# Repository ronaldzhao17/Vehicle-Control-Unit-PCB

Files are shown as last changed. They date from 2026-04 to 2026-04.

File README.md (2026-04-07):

# Vehicle-Control-Unit-PCB Overview
The Vehicle Control Unit PCB (VCU) is a 4-layer PCB designed for the 2025-2026 Formula SAE Competition EV car (FS-4) at UC Santa Cruz. This board serves as the central low-voltage control system for the vehicle and integrates multiple critical functions into a single platform. The board was designed using KiCAD and printed through JLC PCB.
The board mainly serves these purposes:
1. Brake System Plausibility Device (BSPD) and Main Shutdown Circuit:
2. Electronic Throttle Control: Motor control using position pedal sensor inputs
3. Inertial Measurement Unit: Improves FS-4's traction control
4. System Fault Indication: Traction System Status Indicator, ETC.
## PCB
<div align="center">
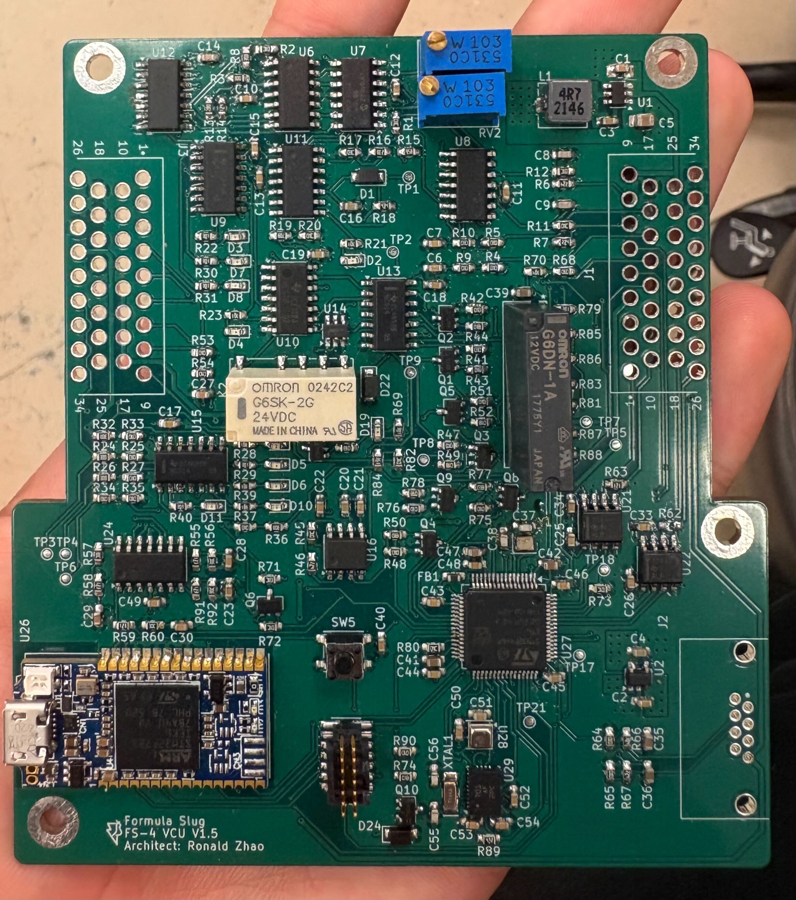
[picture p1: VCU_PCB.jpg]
  
</div>

## Top Layer Signal Diagram
<div align="center">
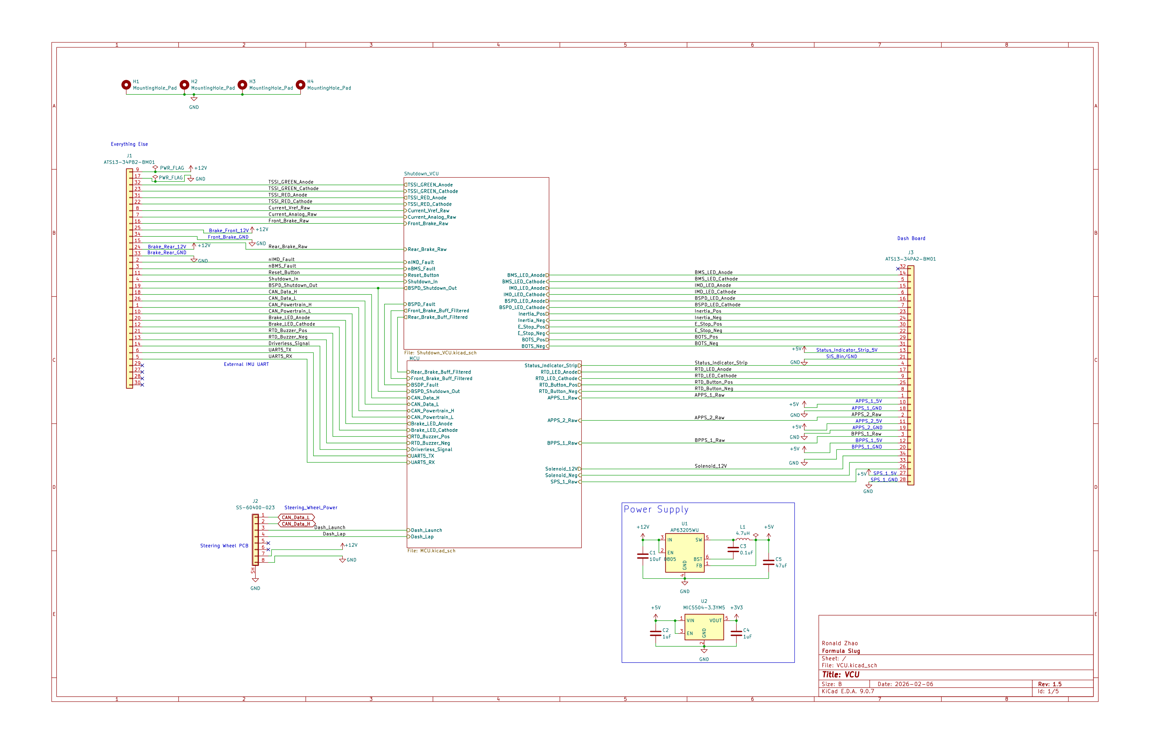
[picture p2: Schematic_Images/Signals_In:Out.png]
  
</div>
The top layer of my schematic is dedicated to present all of the signals inputs and outputs from each connector. It represents a "block diagram" view of the schematic, containing where each of the 60+ signals go.

## BSPD and Shutdown Circuit
<div align="center">
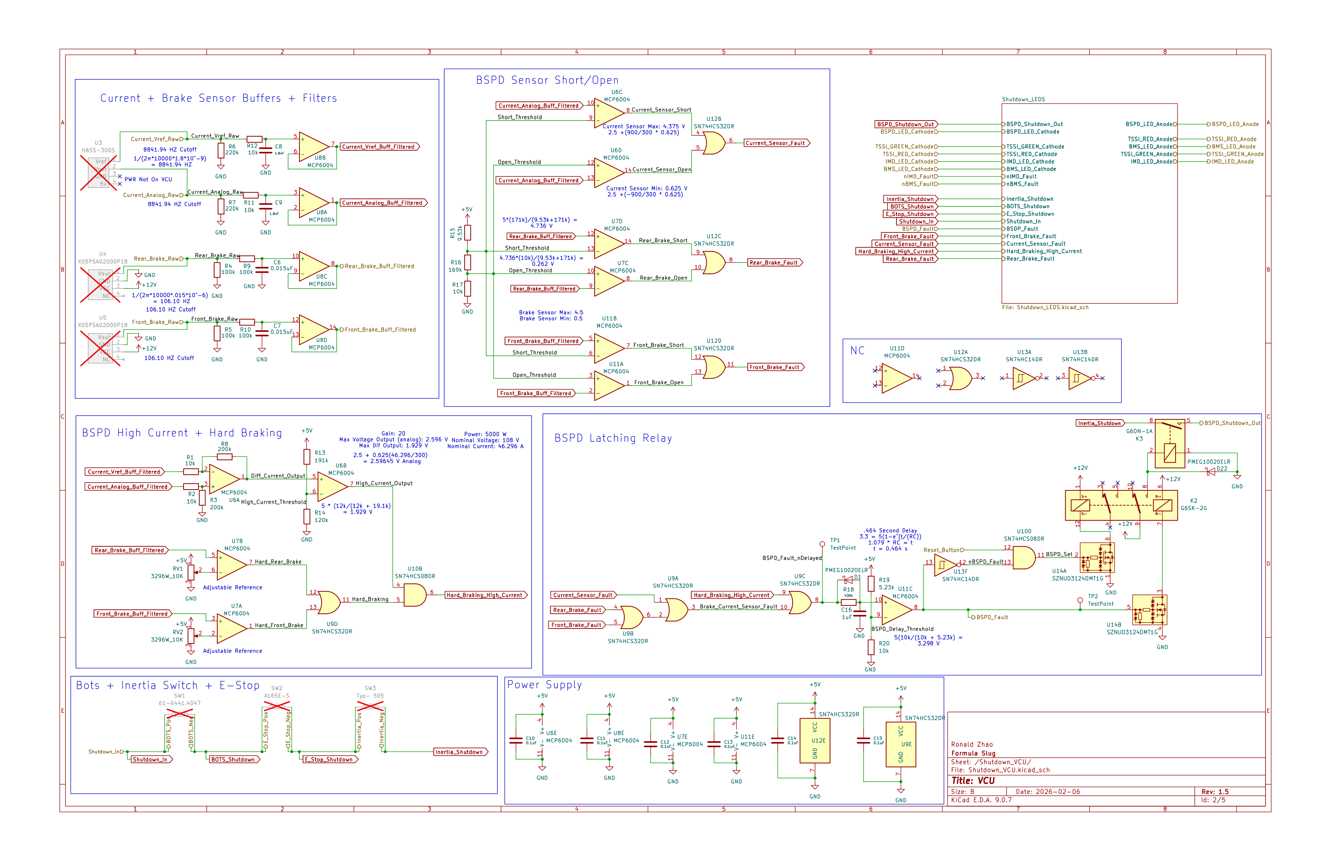
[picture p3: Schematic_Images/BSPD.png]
  
</div>
The brake system plausibility device is a safety mechanism that detects a high current from the motor and active braking. To detect a high current, the output signal from the HASS-300-S current sensor is each filtered to 8841 Hz and buffered. It is then put through a differential amplifier with a gain of 20 in order to obtain a stable, single ended voltage output, as well as a comparator with a voltage threshold based on the reading of the current sensor at our vehicle's nominal current. Similarly, to detect a hard braking, we filter and buffer signals from a pressure sensor for both the front and rear brake. This is compared to a potentiometer we calibrated based on our driver's voltage reading on the pressure sensor while braking. If both of these requirements are fulfilled, then the circuit will output a high, openning our relay connected to the shutdown circuit. Other cases such as the sensor having a short or open circuit also triggers a fault using a series of comparators and logic gates.

## STM32 Microcontroller
<div align="center">
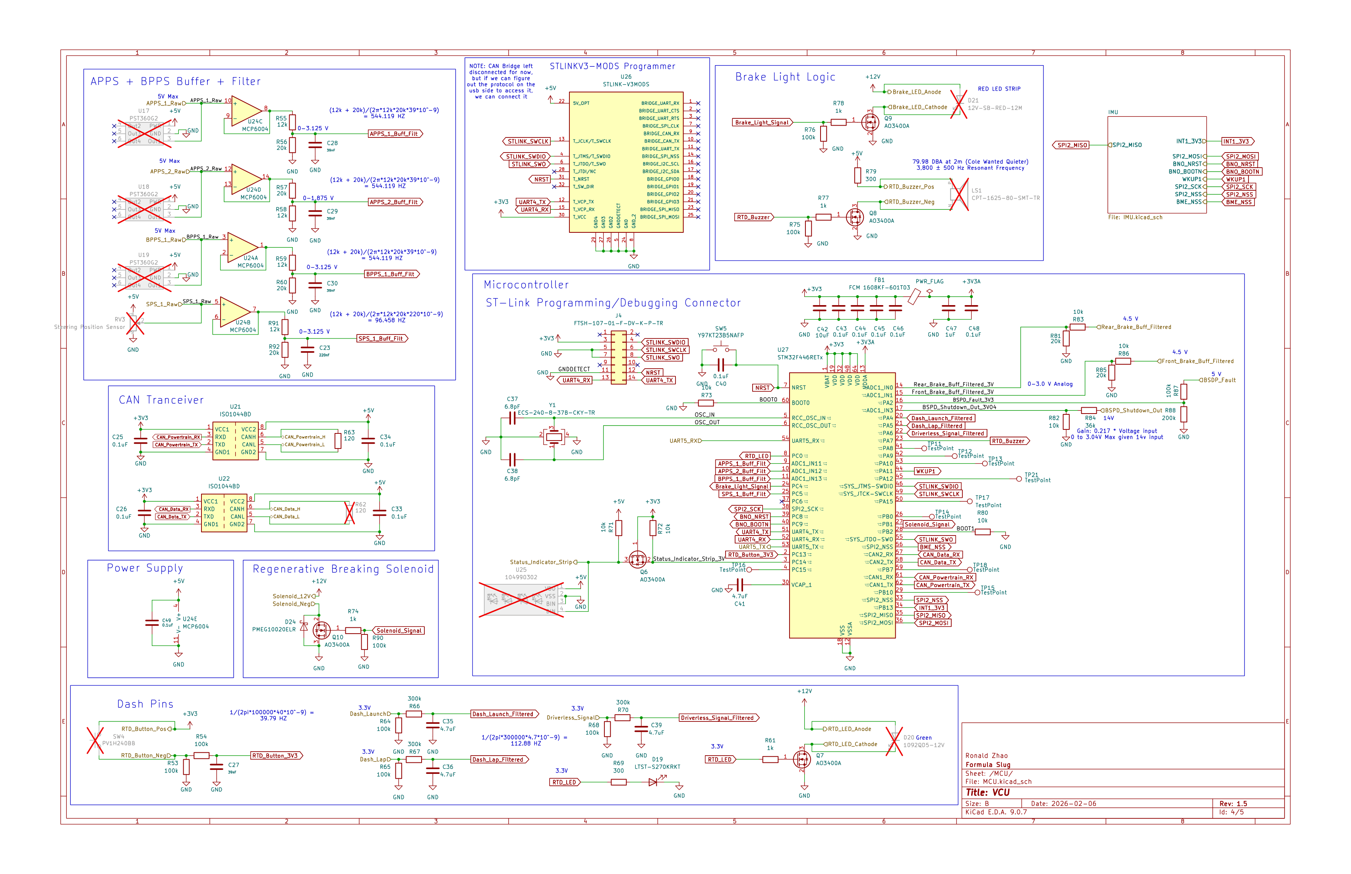
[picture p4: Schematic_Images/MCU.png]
  
</div>
The VCU uses the STM32F446RET6 MCU chip with an external 24 MHz crystal oscillator as its clock, instead previous year's development boards (Nucleos) due to space constraints. The electronic throttle control circuit works by taking in two acceleration pedal position sensor and brake pedal position sensor. This signal is processed by the MCU's firmware and sent through CAN to the motor controller. Other signals going into/out the MCU includes:

- Steering position sensor
- Regenerative Braking Solenoid Signal
- Brake Light
- 2x IMU through SPI and UART
- STLINK V3 MODS Debugger
- Test Points
- Fault Signals

## Inertial Measurement Unit
<div align="center">
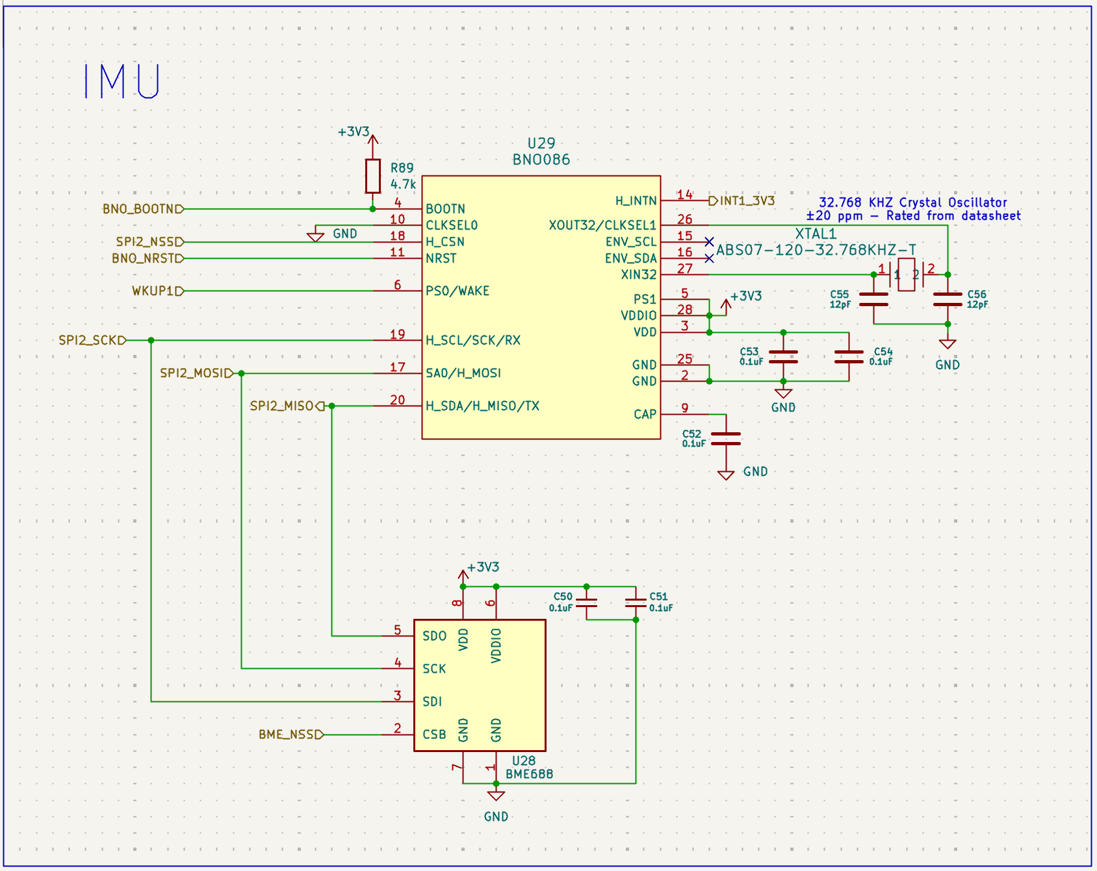
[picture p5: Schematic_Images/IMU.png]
  
</div>
The Inertial Measurement Unit is made up of two sensors to make up the accelerometer, gyroscope, and magnetometer. The IMU uses SPI for its data transfer between the chip and the MCU. Previously our vehicle's traction control was configured to compare the front and rear wheel speed to detect slipping, through our peripheral boards. However, since it requires CAN, the limited bus usage causes the sampling to only be at 100 Hz. This creates a delay and is not practical for quick motor output adjustments. Using the IMU, we can compare both the motor torque output with the car's acceleration (should be proportional) and the steering position sensor's reading with the angular velocity of the car. Since the IMU uses SPI, the sampling rate isn't limited by CAN and has the potential to make precise adjustments.

## Fault Indicators
<div align="center">
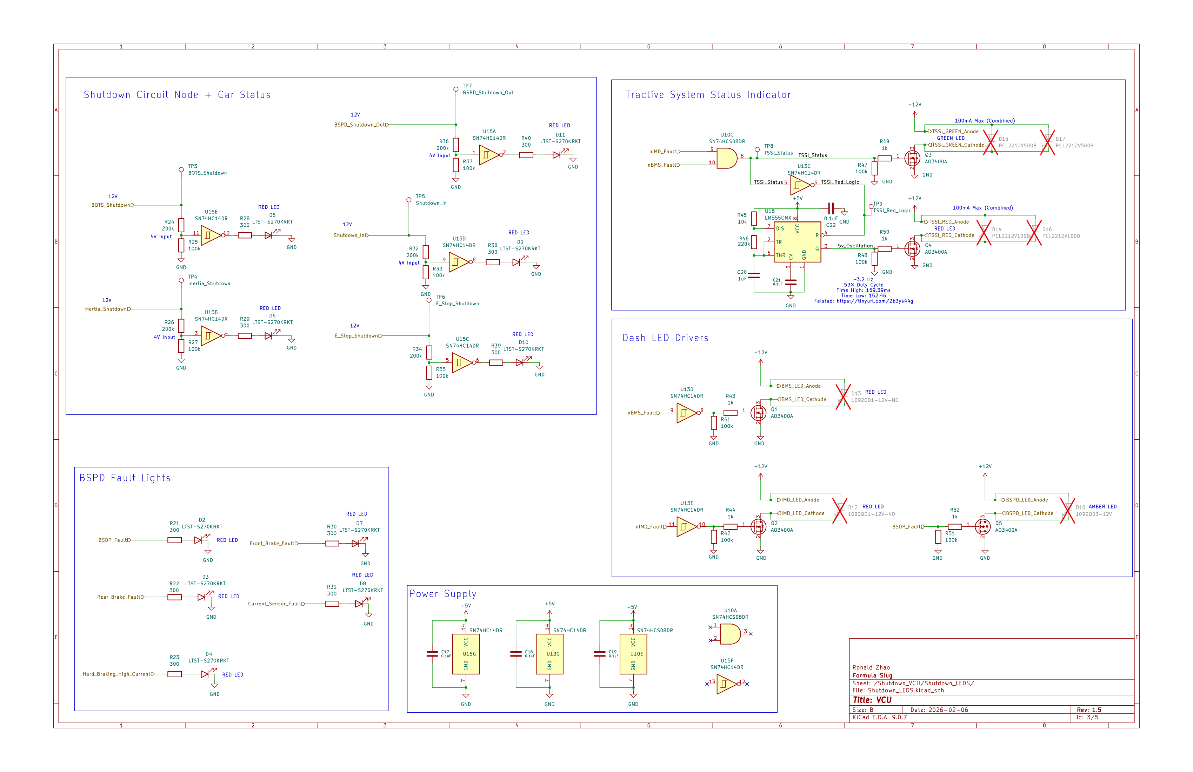
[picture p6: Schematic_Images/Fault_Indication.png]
  
</div>
Fault indicators, such as the Tractive System Status Indicator (TSSI), are required by Formula SAE to signal critical failures in safety-related systems. They also provide a fast method for debugging faults because of their easily accessable test points. These fault lights include:

- IMD
- BMS
- BSPD
- Inertia Switch
- BOTS Switch

## PCB Layout
<div align="center">
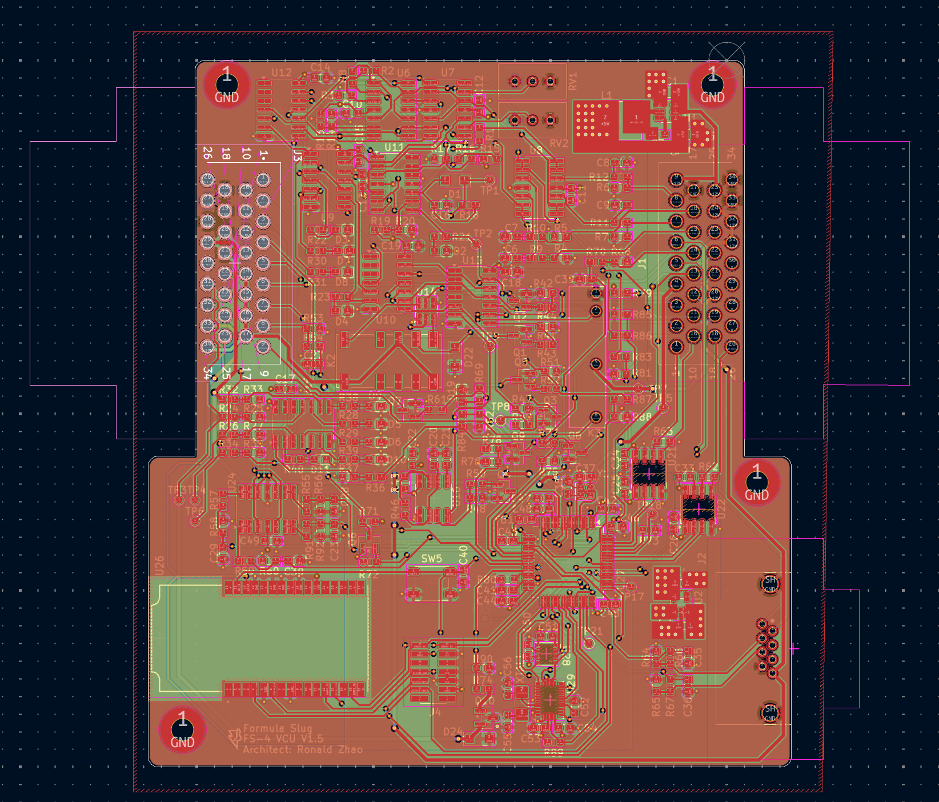
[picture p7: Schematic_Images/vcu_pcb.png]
  
</div>
The layout was done in KiCAD and took almost 6 revisions. It is a 4-layer board with a signal-GND-PWR-signal layer configuration. I started the process by laying out my connectors based on the direction of each respective connectors' signals. Then, I layed out the high speed signals, such as the SPI signal, in a low noise area (far away from DCDC). I kept the traces as short as possible and provided a short return path to reduce the closed loop inductance. The hardest part was placing down my op amps due to the sheer amount of them. To prevent signals crossing, I would often switch the op amp inputs in my schematic. The final design was approved in late February. The end product was a 4x4 inch pcb with over 200 components.

## Soldering, Testing, and Debugging
<div align="center">
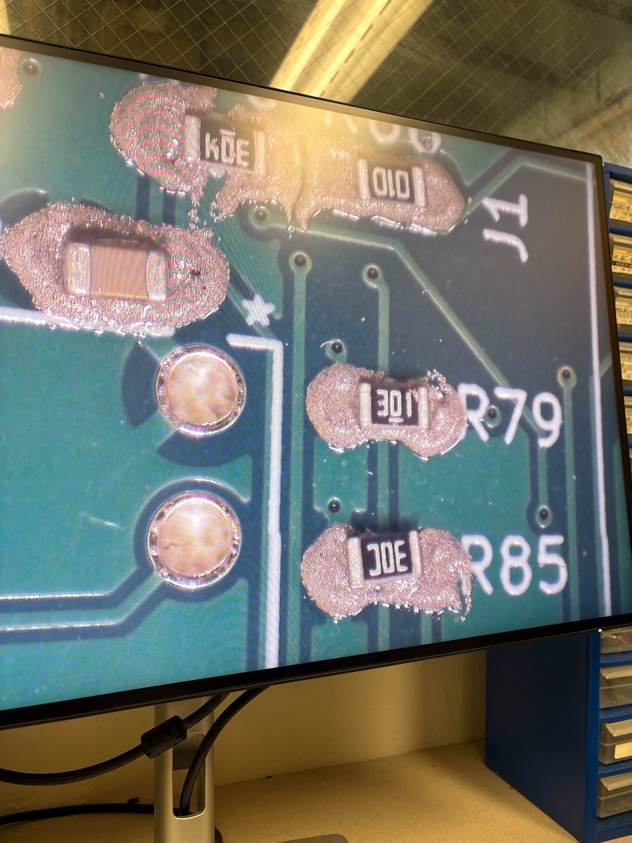
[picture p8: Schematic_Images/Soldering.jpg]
  
</div>
One of the hardest parts of the process was soldering and debugging the board. Almost all of our passive components were 0603 and were entirely hand soldered and the process took over 8 hours. I debugged the board primarily through following my test plan, which you can find here: 

[Test Plan](https://docs.google.com/document/d/1dWHqh_tH-KAfCqI4JE5uINjZ180YYHxUwMFZACGtfho/edit?usp=sharing)

Many of the faults included shorts from the microcontroller and STLINKV3 due to their small pad size. 

## Closing Remarks
This was definitely the biggest, most complex, and my proudest project to date! If you have any questions email me at: ronaldzhao17@gmail.com

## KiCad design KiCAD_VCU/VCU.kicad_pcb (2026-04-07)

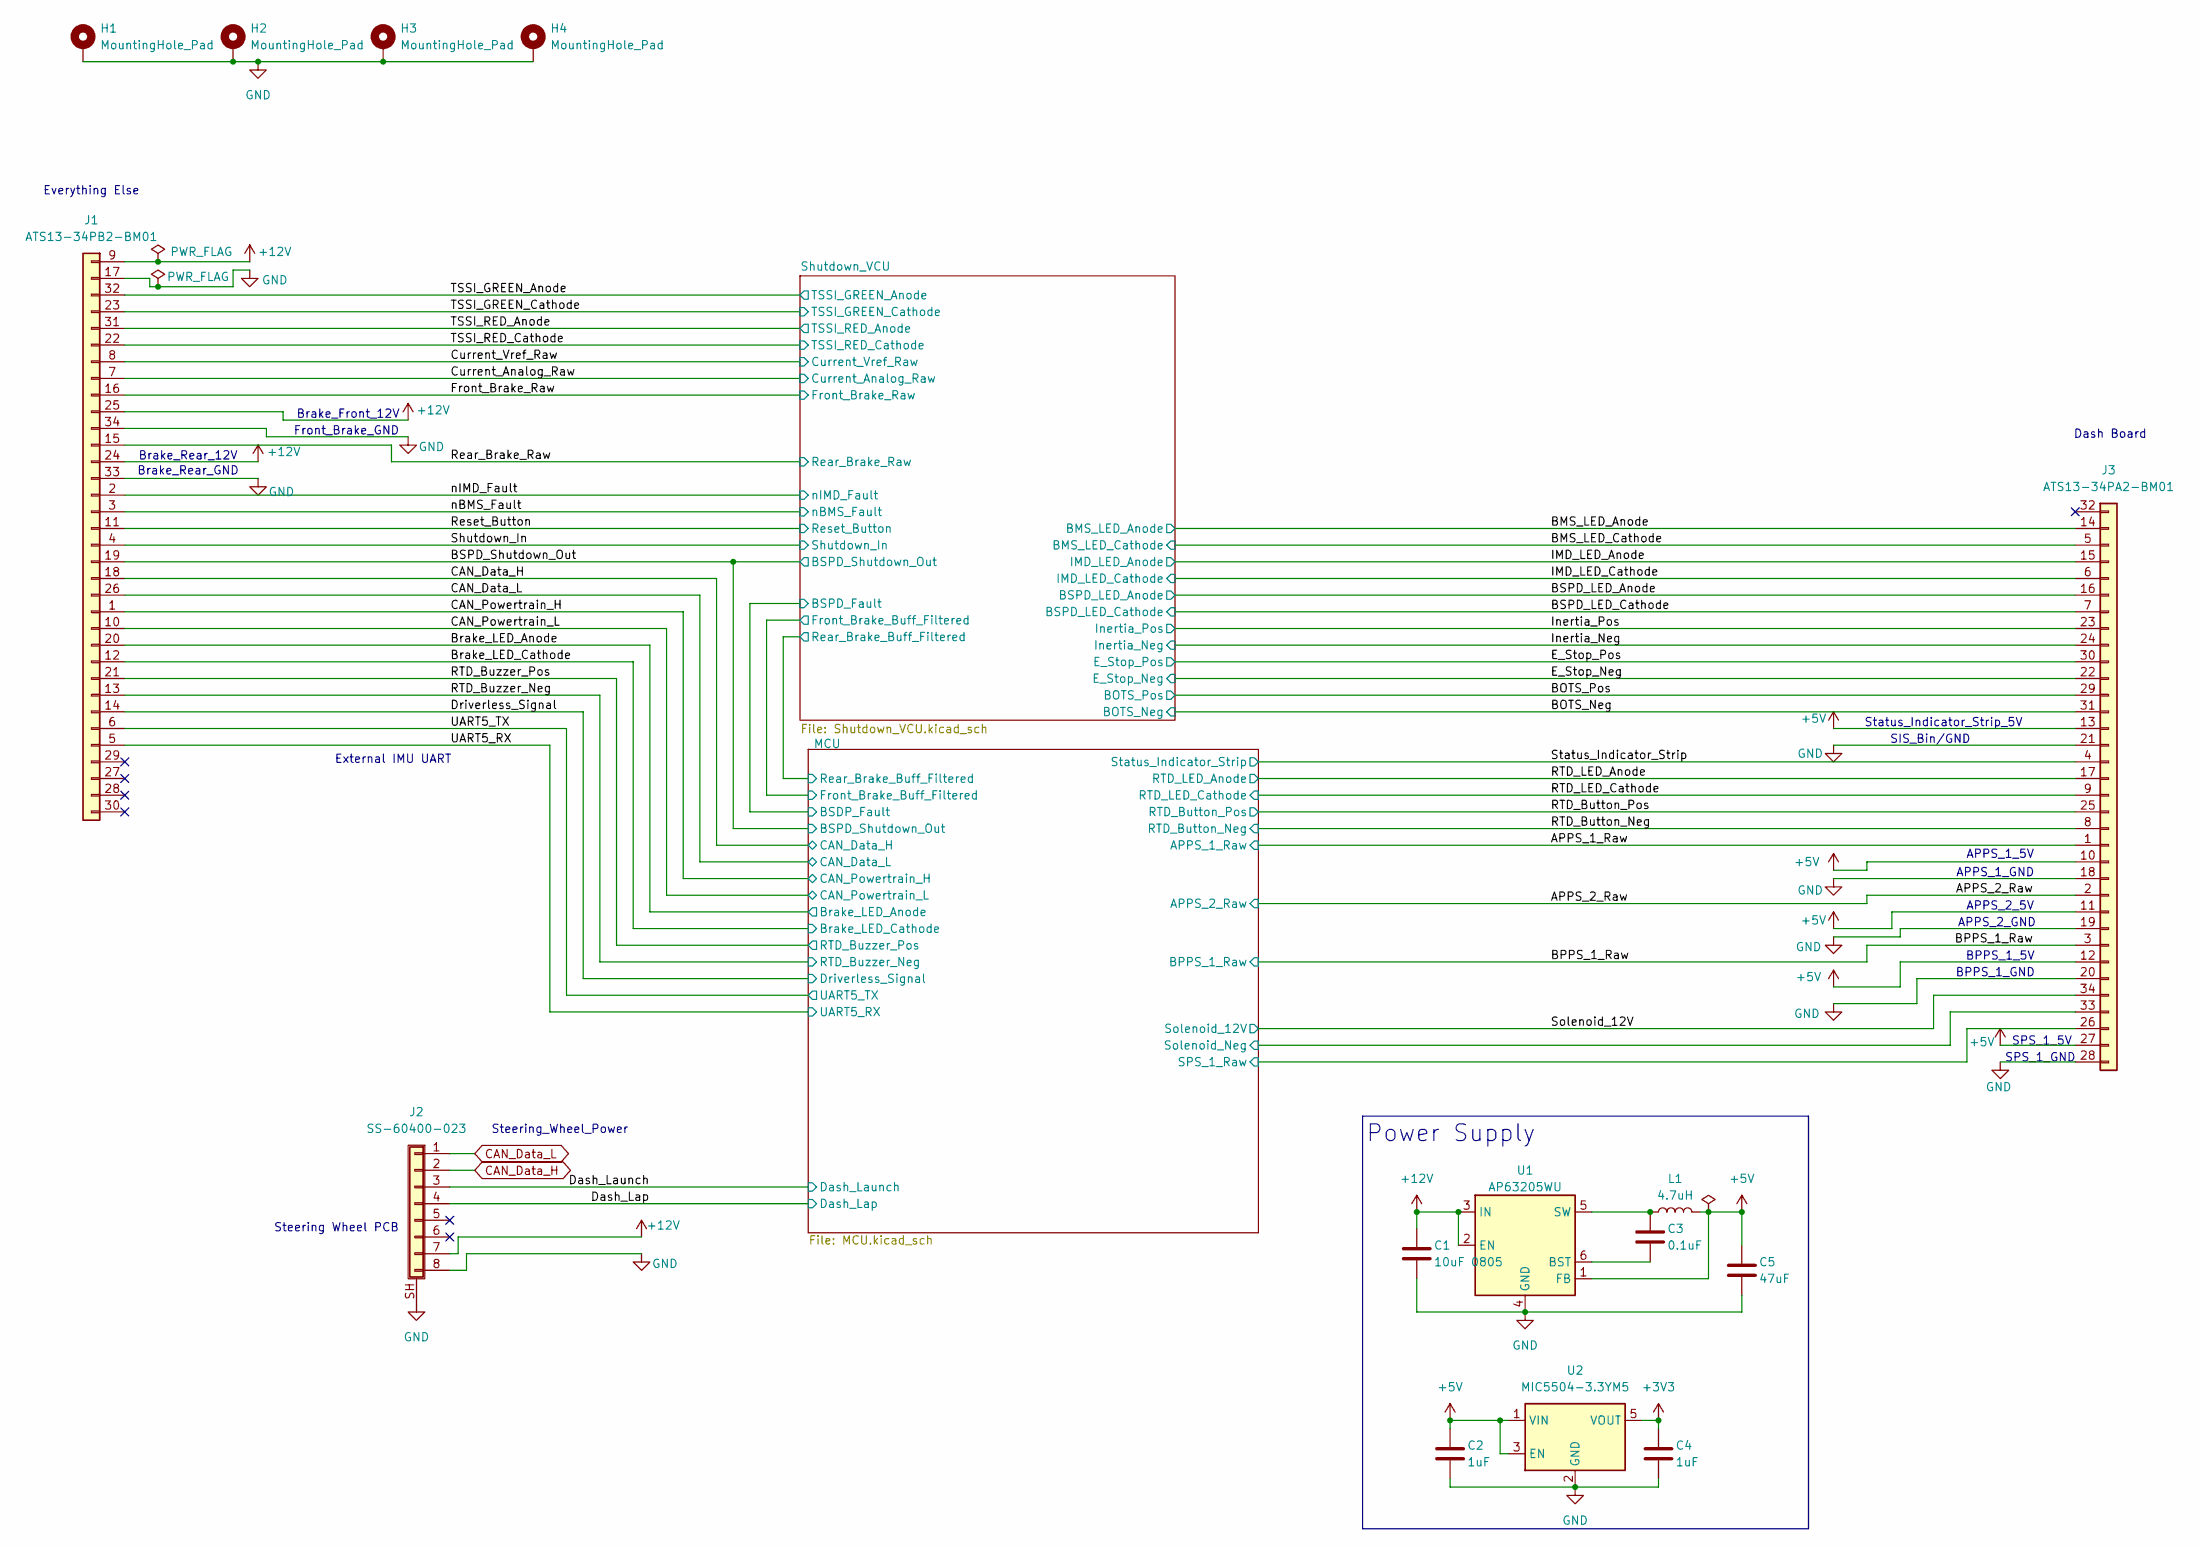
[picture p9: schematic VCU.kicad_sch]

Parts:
C1: 10uF 0805; C_0805_2012Metric_Pad1.18x1.45mm_HandSolder; MFG PN CL21A106KAYNNNE; Digi PN 1276-2891-1-ND
C2, C4: 1uF; C_0603_1608Metric_Pad1.08x0.95mm_HandSolder; MFG PN CC0603JRX7R6BB105; Digi PN 311-3484-1-ND
C3: 0.1uF; C_0603_1608Metric_Pad1.08x0.95mm_HandSolder; MFG PN CC0603JRX7R9BB104; Digi PN 311-1779-1-ND
C5: 47uF; C_0805_2012Metric_Pad1.18x1.45mm_HandSolder; MFG PN CL21A476MQYNNNE; Digi PN 1276-1852-1-ND
H1, H2, H3, H4: MountingHole_Pad; MountingHole_3.2mm_M3_Pad
J1: ATS13-34PB2-BM01; MFG PN ATS13-34PB2-BM01; Digi PN 889-ATS13-34PB2-BM01-ND
J2: SS-60400-023; MFG PN SS-60400-023; Digi PN 380-SS-60400-023-ND
J3: ATS13-34PA2-BM01; MFG PN ATS13-34PA2-BM01; Digi PN 889-ATS13-34PA2-BM01-ND
L1: 4.7uH; L_Bourns_SRP5030T; MFG PN SRP5030TA-4R7M; Digi PN SRP5030TA-4R7MCT-ND
U1: AP63205WU; TSOT-23-6; MFG PN AP63205WU-7; Digi PN AP63205WU-7DICT-ND
U2: MIC5504-3.3YM5; SOT-23-5; MFG PN MIC5504-3.3YM5-TR; Digi PN 576-4764-1-ND

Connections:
+3V3: C4.2, J3.25, U2.5 (VOUT); also elsewhere on the board
+5V: C2.2, C5.2, J3.10, J3.11, J3.12, J3.13, J3.27, L1.2, U1.1 (FB), U2.1 (VIN), U2.3 (EN); also elsewhere on the board
+12V: C1.2, J1.9, J1.20, J1.24, J1.25, J1.31, J1.32, J2.7, J3.14, J3.15, J3.16, J3.17, J3.34, U1.2 (EN), U1.3 (IN); also elsewhere on the board
/APPS_1_Raw: J3.1; also elsewhere on the board
/APPS_2_Raw: J3.2; also elsewhere on the board
/BMS_LED_Cathode: J3.5; also elsewhere on the board
/BPPS_1_Raw: J3.3; also elsewhere on the board
/BSPD_LED_Cathode: J3.7; also elsewhere on the board
/Brake_LED_Cathode: J1.12; also elsewhere on the board
/CAN_Powertrain_H: J1.1; also elsewhere on the board
/CAN_Powertrain_L: J1.10; also elsewhere on the board
/Current_Analog_Raw: J1.7; also elsewhere on the board
/Current_Vref_Raw: J1.8; also elsewhere on the board
/Dash_Lap: J2.4; also elsewhere on the board
/Dash_Launch: J2.3; also elsewhere on the board
/Driverless_Signal: J1.14; also elsewhere on the board
/Front_Brake_Raw: J1.16; also elsewhere on the board
/IMD_LED_Cathode: J3.6; also elsewhere on the board
/MCU/SPS_1_Raw: J3.26; also elsewhere on the board
/MCU/Solenoid_Neg: J3.33; also elsewhere on the board
/RTD_Button_Neg: J3.8; also elsewhere on the board
/RTD_Buzzer_Neg: J1.13; also elsewhere on the board
/RTD_Buzzer_Pos: J1.21; also elsewhere on the board
/RTD_LED_Cathode: J3.9; also elsewhere on the board
/Rear_Brake_Raw: J1.15; also elsewhere on the board
/Reset_Button: J1.11; also elsewhere on the board
/Status_Indicator_Strip: J3.4; also elsewhere on the board
/TSSI_GREEN_Cathode: J1.23; also elsewhere on the board
/TSSI_RED_Cathode: J1.22; also elsewhere on the board
/UART5_RX: J1.5; also elsewhere on the board
/UART5_TX: J1.6; also elsewhere on the board
/nBMS_Fault: J1.3; also elsewhere on the board
/nIMD_Fault: J1.2; also elsewhere on the board
BOTS_Shutdown: J3.30, J3.31; also elsewhere on the board
BSPD_Shutdown_Out: J1.19; also elsewhere on the board
CAN_Data_H: J1.18, J2.2; also elsewhere on the board
CAN_Data_L: J1.26, J2.1; also elsewhere on the board
E_Stop_Shutdown: J3.22, J3.23; also elsewhere on the board
GND: C1.1, C2.1, C4.1, C5.1, H1.1, H2.1, H3.1, H4.1, J1.17, J1.33, J1.34, J2.8, J2.SH (Shield), J3.18, J3.19, J3.20, J3.21, J3.28, U1.4 (GND), U2.2 (GND); also elsewhere on the board
Inertia_Shutdown: J3.24; also elsewhere on the board
unnamed: C3.1, U1.6 (BST)
unnamed: C3.2, L1.1, U1.5 (SW)
Shutdown_In: J1.4, J3.29; also elsewhere on the board

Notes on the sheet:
Brake_Front_12V
External IMU UART
APPS_2_5V
BPPS_1_5V
Front_Brake_GND
APPS_2_GND
Dash Board
Steering Wheel PCB
Steering_Wheel_Power
Status_Indicator_Strip_5V
Everything Else
Brake_Rear_12V
SPS_1_GND
Brake_Rear_GND
Power Supply
APPS_1_GND
SIS_Bin/GND
BPPS_1_GND
APPS_1_5V
SPS_1_5V

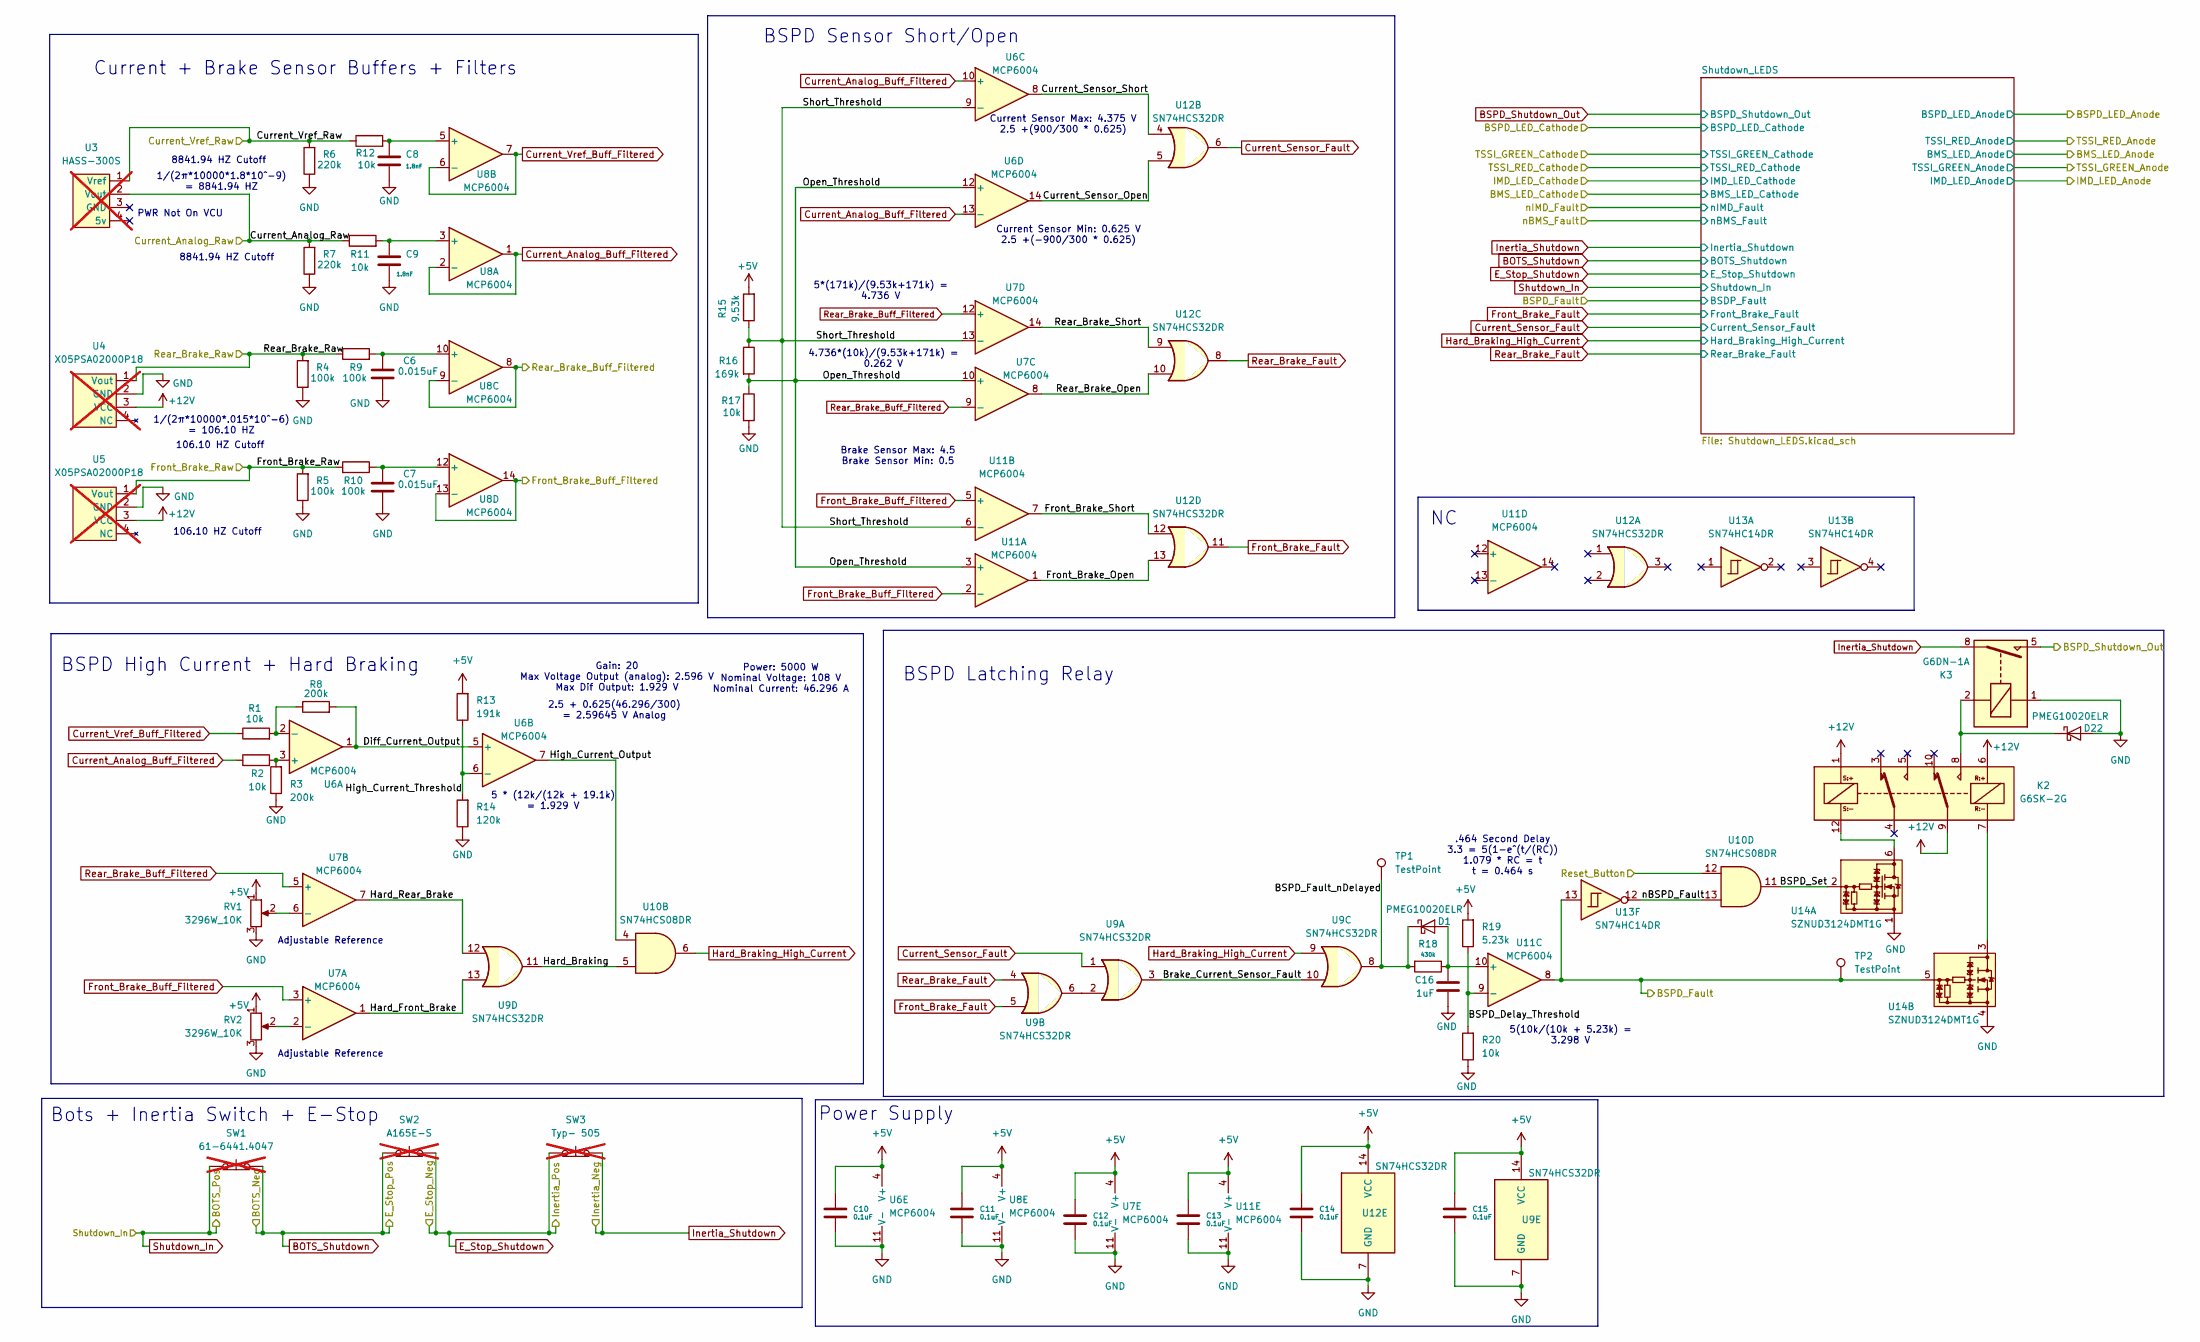
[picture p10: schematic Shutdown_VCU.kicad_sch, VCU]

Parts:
C6, C7: 0.015uF; C_0603_1608Metric_Pad1.08x0.95mm_HandSolder; MFG PN CC0603KRX7R9BB153; Digi PN 311-1430-1-ND
C8, C9: 1.8nF; C_0603_1608Metric_Pad1.08x0.95mm_HandSolder; MFG PN CC0603FRNPO9BN182; Digi PN 13-CC0603FRNPO9BN182CT-ND
C10, C11, C12, C13, C14, C15: 0.1uF; C_0603_1608Metric_Pad1.08x0.95mm_HandSolder; MFG PN CC0603JRX7R9BB104; Digi PN 311-1779-1-ND
C16: 1uF; C_0603_1608Metric_Pad1.08x0.95mm_HandSolder; MFG PN CC0603JRX7R6BB105; Digi PN 311-3484-1-ND
D1, D22: PMEG10020ELR; Nexperia_CFP3_SOD-123W; MFG PN PMEG10020ELR-QX; Digi PN 1727-PMEG10020ELR-QXCT-ND
K2: G6SK-2G; Relay_DPDT_Omron_G6SK-2G; MFG PN G6SK-2G DC24; Digi PN Z12726-ND
K3: G6DN-1A; RELAY_G6DN-1A; MFG PN G6DN-1A DC12; Digi PN Z5440-ND
R1, R2, R11, R12, R17, R20: 10k; R_0603_1608Metric_Pad0.98x0.95mm_HandSolder; MFG PN AC0603FR-0710KL; Digi PN 311-10KLDCT-ND
R3, R8: 200k; R_0603_1608Metric_Pad0.98x0.95mm_HandSolder; MFG PN AC0603FR-07200KL; Digi PN YAG3575CT-ND
R4, R5, R9, R10: 100k; R_0603_1608Metric_Pad0.98x0.95mm_HandSolder; MFG PN AC0603FR-13100KL; Digi PN 13-AC0603FR-13100KLCT-ND
R6, R7: 220k; R_0603_1608Metric_Pad0.98x0.95mm_HandSolder; MFG PN AC0603FR-07220KL; Digi PN YAG3579CT-ND
R13: 191k; R_0603_1608Metric_Pad0.98x0.95mm_HandSolder; MFG PN AC0603FR-07191KL; Digi PN 13-AC0603FR-07191KLCT-ND
R14: 120k; R_0603_1608Metric_Pad0.98x0.95mm_HandSolder; MFG PN AC0603FR-07120KL; Digi PN YAG3562CT-ND
R15: 9.53k; R_0603_1608Metric_Pad0.98x0.95mm_HandSolder; MFG PN AC0603FR-079K53L; Digi PN 13-AC0603FR-079K53LCT-ND
R16: 169k; R_0603_1608Metric_Pad0.98x0.95mm_HandSolder; MFG PN AC0603FR-07169KL; Digi PN 13-AC0603FR-07169KLCT-ND
R18: 430k; R_0603_1608Metric_Pad0.98x0.95mm_HandSolder; MFG PN AC0603FR-07430KL; Digi PN 13-AC0603FR-07430KLCT-ND
R19: 5.23k; R_0603_1608Metric_Pad0.98x0.95mm_HandSolder; MFG PN AC0603FR-075K23L; Digi PN 13-AC0603FR-075K23LCT-ND
RV1, RV2: 3296W_10K; Potentiometer_Bourns_3296W_Vertical; MFG PN 3296W-1-103LF; Digi PN 3296W-103LF-ND
SW1: 61-6441.4047; MFG PN 61-6441.4047; Digi PN 1948-1780-ND; not fitted
SW2: A165E-S; MFG PN A165E-S; Digi PN Z8879-ND; not fitted
SW3: Typ- 505; not fitted
TP1, TP2: TestPoint; TestPoint_Pad_D1.0mm
U3: HASS-300S; MFG PN HASS 300-S; Digi PN 398-1065-ND; not fitted
U4, U5: X05PSA02000P18; not fitted
U6, U7, U8, U11: MCP6004; SOIC-14_3.9x8.7mm_P1.27mm; MFG PN MCP6004T-I/SL; Digi PN MCP6004T-I/SLCT-ND
U9, U12: SN74HCS32DR; SOIC-14_3.9x8.7mm_P1.27mm; MFG PN SN74HCS32DR; Digi PN 296-SN74HCS32DRCT-ND
U10: SN74HCS08DR; SOIC-14_3.9x8.7mm_P1.27mm; MFG PN SN74HCS08DR; Digi PN 296-SN74HCS08DRCT-ND
U13: SN74HC14DR; SOIC-14_3.9x8.7mm_P1.27mm; MFG PN SN74HC14DR; Digi PN 296-1194-1-ND
U14: SZNUD3124DMT1G; SC-74-6_1.55x2.9mm_P0.95mm; MFG PN SZNUD3124DMT1G; Digi PN SZNUD3124DMT1GOSCT-ND

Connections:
+5V: C10.1, C11.1, C12.1, C13.1, C14.1, C15.1, R13.2, R15.2, R19.2, RV1.1, RV2.1, U6.4 (V+), U7.4 (V+), U8.4 (V+), U9.14 (VCC), U11.4 (V+), U12.14 (VCC); also elsewhere on the board
+12V: K2.1, K2.6, K2.9, U4.3 (VCC), U5.3 (VCC); also elsewhere on the board
/Current_Analog_Raw: R7.2, R11.1, U3.2 (Vout); also elsewhere on the board
/Current_Vref_Raw: R6.2, R12.1, U3.1 (Vref); also elsewhere on the board
/Front_Brake_Raw: R5.2, R10.2, U5.1 (Vout); also elsewhere on the board
/MCU/BSDP_Fault: TP2.1, U11.8, U13.13, U14.5; also elsewhere on the board
/Rear_Brake_Raw: R4.2, R9.1, U4.1 (Vout); also elsewhere on the board
/Reset_Button: U10.12; also elsewhere on the board
/Shutdown_VCU/BSPD_Delay_Threshold: R19.1, R20.2, U11.9 (-)
/Shutdown_VCU/BSPD_Fault_nDelayed: D1.1 (K), R18.2, TP1.1, U9.8
/Shutdown_VCU/BSPD_Set: U10.11, U14.2
/Shutdown_VCU/Brake_Current_Sensor_Fault: U9.3, U9.10
/Shutdown_VCU/Current_Sensor_Open: U6.14, U12.5
/Shutdown_VCU/Current_Sensor_Short: U6.8, U12.4
/Shutdown_VCU/Diff_Current_Output: R8.2, U6.1, U6.5 (+)
/Shutdown_VCU/Front_Brake_Open: U11.1, U12.13
/Shutdown_VCU/Front_Brake_Short: U11.7, U12.12
/Shutdown_VCU/Hard_Braking: U9.11, U10.5
/Shutdown_VCU/Hard_Front_Brake: U7.1, U9.13
/Shutdown_VCU/Hard_Rear_Brake: U7.7, U9.12
/Shutdown_VCU/High_Current_Output: U6.7, U10.4
/Shutdown_VCU/High_Current_Threshold: R13.1, R14.2, U6.6 (-)
/Shutdown_VCU/Open_Threshold: R16.2, R17.1, U6.12 (+), U7.10 (+), U11.3 (+)
/Shutdown_VCU/Rear_Brake_Open: U7.8, U12.10
/Shutdown_VCU/Rear_Brake_Short: U7.14, U12.9
/Shutdown_VCU/Short_Threshold: R15.1, R16.1, U6.9 (-), U7.13 (-), U11.6 (-)
/Shutdown_VCU/nBSPD_Fault: U10.13, U13.12
BSPD_Shutdown_Out: K3.5; also elsewhere on the board
Current_Analog_Buff_Filtered: R2.1, U6.10 (+), U6.13 (-), U8.1, U8.2 (-)
Current_Sensor_Fault: U9.1, U12.6; also elsewhere on the board
Current_Vref_Buff_Filtered: R1.1, U8.6 (-), U8.7
Front_Brake_Buff_Filtered: U7.3 (+), U8.13 (-), U8.14, U11.2 (-), U11.5 (+); also elsewhere on the board
Front_Brake_Fault: U9.5, U12.11; also elsewhere on the board
GND: C6.2, C7.2, C8.2, C9.2, C10.2, C11.2, C12.2, C13.2, C14.2, C15.2, C16.1, D22.2 (A), K3.1, R3.1, R4.1, R5.1, R6.1, R7.1, R14.1, R17.2, R20.1, RV1.3, RV2.3, U4.2 (GND), U5.2 (GND), U6.11 (V-), U7.11 (V-), U8.11 (V-), U9.7 (GND), U11.11 (V-), U12.7 (GND), U14.1, U14.4; also elsewhere on the board
Hard_Braking_High_Current: U9.9, U10.6; also elsewhere on the board
Inertia_Shutdown: K3.8, SW3.2 (B); also elsewhere on the board
unnamed: C16.2, D1.2 (A), R18.1, U11.10 (+)
unnamed: D22.1 (K), K2.8, K3.2
unnamed: K2.7, U14.3
unnamed: K2.12, U14.6
unnamed: SW1.2 (B), SW2.1 (A)
unnamed: SW2.2 (B), SW3.1 (A)
unnamed: R2.2, R3.2, U6.3 (+)
unnamed: R1.2, R8.1, U6.2 (-)
unnamed: RV2.2, U7.2 (-)
unnamed: RV1.2, U7.6 (-)
unnamed: C9.1, R11.2, U8.3 (+)
unnamed: C8.1, R12.2, U8.5 (+)
unnamed: C6.1, R9.2, U8.10 (+)
unnamed: C7.1, R10.1, U8.12 (+)
unnamed: U9.2, U9.6
Rear_Brake_Buff_Filtered: U7.5 (+), U7.9 (-), U7.12 (+), U8.8, U8.9 (-); also elsewhere on the board
Rear_Brake_Fault: U9.4, U12.8; also elsewhere on the board

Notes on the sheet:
1/(2π*10000*.015*10^-6) = 106.10 HZ
Power Supply
Current Sensor Max: 4.375 V 2.5 +(900/300 * 0.625)
Gain: 20 Max Voltage Output (analog): 2.596 V Max Dif Output: 1.929 V
Power: 5000 W Nominal Voltage: 108 V Nominal Current: 46.296 A
106.10 HZ Cutoff
Adjustable Reference
1/(2π*10000*1.8*10^-9) = 8841.94 HZ
8841.94 HZ Cutoff
5 * (12k/(12k + 19.1k) = 1.929 V
BSPD Latching Relay
5(10k/(10k + 5.23k) = 3.298 V
Current + Brake Sensor Buffers + Filters
.464 Second Delay 3.3 = 5(1-e^(t/(RC)) 1.079 * RC = t t = 0.464 s
BSPD Sensor Short/Open
2.5 + 0.625(46.296/300) = 2.59645 V Analog
4.736*(10k)/(9.53k+171k) = 0.262 V
Brake Sensor Max: 4.5 Brake Sensor Min: 0.5
Current Sensor Min: 0.625 V 2.5 +(-900/300 * 0.625)
Bots + Inertia Switch + E-Stop
5*(171k)/(9.53k+171k) = 4.736 V
BSPD High Current + Hard Braking
PWR Not On VCU

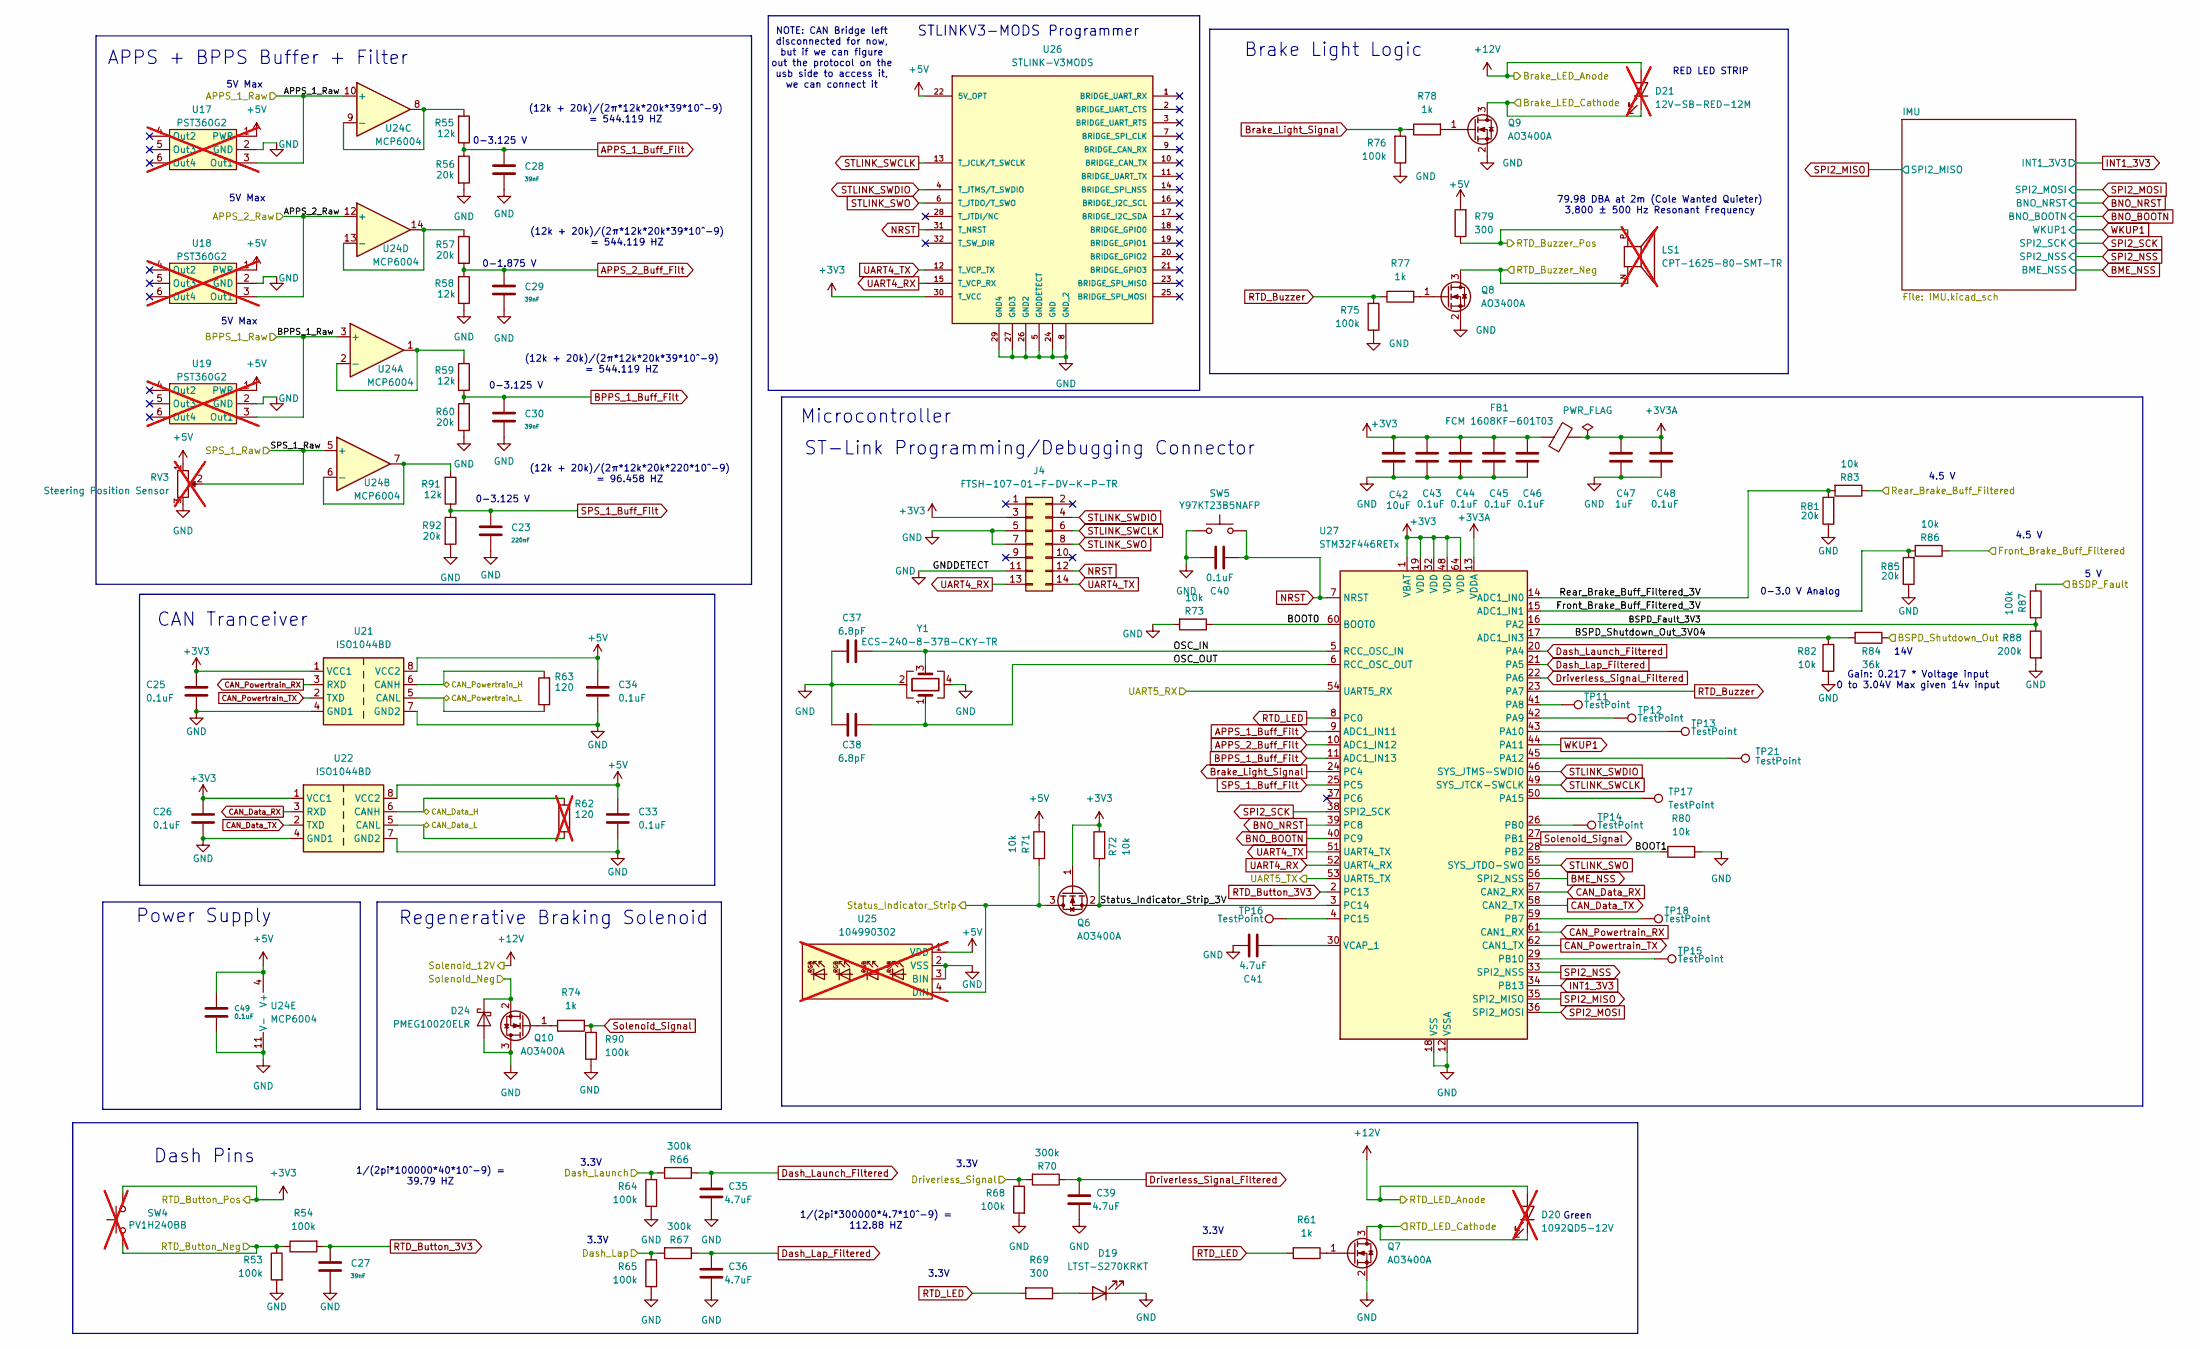
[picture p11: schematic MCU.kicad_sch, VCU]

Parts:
C23: 220nF; C_0603_1608Metric_Pad1.08x0.95mm_HandSolder; MFG PN CC0603KRX7R8BB224; Digi PN 311-1803-1-ND
C25, C26, C33, C34, C40, C43, C44, C45, C46, C48, C49: 0.1uF; C_0603_1608Metric_Pad1.08x0.95mm_HandSolder; MFG PN CC0603JRX7R9BB104; Digi PN 311-1779-1-ND
C27, C28, C29, C30: 39nF; C_0603_1608Metric_Pad1.08x0.95mm_HandSolder; MFG PN CC0603JRX7R9BB393; Digi PN 13-CC0603JRX7R9BB393CT-ND
C35, C36, C39, C41: 4.7uF; C_0603_1608Metric_Pad1.08x0.95mm_HandSolder; MFG PN CL10A475KL8NRNC; Digi PN 1276-6794-1-ND
C37, C38: 6.8pF; C_0603_1608Metric_Pad1.08x0.95mm_HandSolder; MFG PN CC0603DRNPO9BN6R8; Digi PN 311-3874-1-ND
C42: 10uF; C_0603_1608Metric_Pad1.08x0.95mm_HandSolder; MFG PN CL10A106KO8NQNC; Digi PN 1276-CL10A106KO8NQNCCT-ND
C47: 1uF; C_0603_1608Metric_Pad1.08x0.95mm_HandSolder; MFG PN CC0603JRX7R6BB105; Digi PN 311-3484-1-ND
D19: LTST-S270KRKT; LED_0603_1608Metric_Pad1.05x0.95mm_HandSolder; MFG PN LTST-S270KRKT; Digi PN 160-1479-1-ND
D20: 1092QD5-12V; MFG PN 1092QD5-12V; Digi PN 1092QD5-12V-ND; not fitted
D21: 12V-SB-RED-12M; MFG PN 12V-SB-RED-12M; Digi PN 1647-12V-SB-RED-12MCT-ND; not fitted
D24: PMEG10020ELR; Nexperia_CFP3_SOD-123W; MFG PN PMEG10020ELR-QX; Digi PN 1727-PMEG10020ELR-QXCT-ND
FB1: FCM 1608KF-601T03; L_0603_1608Metric_Pad1.05x0.95mm_HandSolder; MFG PN FCM 1608KF-601T03; Digi PN 4816-FCM1608KF-601T03CT-ND
J4: FTSH-107-01-F-DV-K-P-TR; PinHeader_2x07_P1.27mm_Vertical_SMD; MFG PN FTSH-107-01-F-DV-K-P-TR; Digi PN SAM13170CT-ND
LS1: CPT-1625-80-SMT-TR; MFG PN AI-3238-TF-LW140-R; Digi PN 668-1277-ND; not fitted
Q6, Q7, Q8, Q9, Q10: AO3400A; SOT-23; MFG PN AO3400A; Digi PN 785-1000-1-ND
R53, R54, R64, R65, R68, R75, R76, R87, R90: 100k; R_0603_1608Metric_Pad0.98x0.95mm_HandSolder; MFG PN AC0603FR-13100KL; Digi PN 13-AC0603FR-13100KLCT-ND
R55, R58, R59, R91: 12k; R_0603_1608Metric_Pad0.98x0.95mm_HandSolder; MFG PN AC0603FR-1012KL; Digi PN 13-AC0603FR-1012KLCT-ND
R56, R57, R60, R81, R85, R92: 20k; R_0603_1608Metric_Pad0.98x0.95mm_HandSolder; MFG PN AC0603FR-0720KL; Digi PN YAG3577CT-ND
R61, R74, R77, R78: 1k; R_0603_1608Metric_Pad0.98x0.95mm_HandSolder; MFG PN RC0603FR-071KL; Digi PN 311-1.00KHRCT-ND
R62: 120; R_0603_1608Metric_Pad0.98x0.95mm_HandSolder; MFG PN AC0603FR-07120RL; Digi PN YAG3563CT-ND; not fitted
R63: 120; R_0603_1608Metric_Pad0.98x0.95mm_HandSolder; MFG PN AC0603FR-07120RL; Digi PN YAG3563CT-ND
R66, R67, R70: 300k; R_0603_1608Metric_Pad0.98x0.95mm_HandSolder; MFG PN AC0603FR-07300KL; Digi PN 13-AC0603FR-07300KLCT-ND
R69, R79: 300; R_0603_1608Metric_Pad0.98x0.95mm_HandSolder; MFG PN AC0603FR-07300RL; Digi PN YAG5330CT-ND
R71, R72, R73, R80, R82, R83, R86: 10k; R_0603_1608Metric_Pad0.98x0.95mm_HandSolder; MFG PN AC0603FR-0710KL; Digi PN 311-10KLDCT-ND
R84: 36k; R_0603_1608Metric_Pad0.98x0.95mm_HandSolder; MFG PN AC0603FR-0736KL; Digi PN 13-AC0603FR-0736KLCT-ND
R88: 200k; R_0603_1608Metric_Pad0.98x0.95mm_HandSolder; MFG PN AC0603FR-07200KL; Digi PN YAG3575CT-ND
RV3: Steering Position Sensor; not fitted
SW4: PV1H240BB; SW_SPST_PTS647_Sx38; MFG PN PV1H240BB; Digi PN EG5277-ND; not fitted
SW5: Y97KT23B5NAFP; SW_SPST_PTS647_Sx38; MFG PN Y97KT23B5NAFP; Digi PN 108-Y97KT23B5NAFPCT-ND
TP11, TP12, TP13, TP14, TP15, TP16, TP17, TP18, TP21: TestPoint; TestPoint_Pad_D1.0mm
U17, U18, U19: PST360G2; MFG PN PST360G2-1A-C0000-ERA360-05K; Digi PN 1993-1011-ND; not fitted
U21, U22: ISO1044BD; SOIC-8_ISO1044BD; MFG PN ISO1044BDR; Digi PN 296-ISO1044BDRCT-ND
U24: MCP6004; SOIC-14_3.9x8.7mm_P1.27mm; MFG PN MCP6004T-I/SL; Digi PN MCP6004T-I/SLCT-ND
U25: 104990302; MFG PN 104990302; Digi PN 1597-1485-ND; not fitted
U26: STLINK-V3MODS; MODULE_STLINK-V3MODS; PARTREV 1; Digi PN 497-STLINK-V3MODS-ND
U27: STM32F446RETx; LQFP-64_10x10mm_P0.5mm; MFG PN STM32F446RET6; Digi PN 497-15376-ND
Y1: ECS-240-8-37B-CKY-TR; Crystal_SMD_2016-4Pin_2.0x1.6mm; MFG PN ECS-240-8-37B-CKY-TR; Digi PN XC3063CT-ND

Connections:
+3V3: C25.1, C26.1, C42.2, C43.1, C44.1, C45.1, C46.1, FB1.1, J4.3, Q6.1 (G), R72.2, SW4.2, U21.1 (VCC1), U22.1 (VCC1), U26.30 (T_VCC), U27.1 (VBAT), U27.19 (VDD), U27.32 (VDD), U27.48 (VDD), U27.64 (VDD); also elsewhere on the board
+3V3A: C47.1, C48.1, FB1.2, U27.13 (VDDA)
+5V: C33.1, C34.1, C49.1, R71.1, R79.2, RV3.1, U17.1 (PWR), U18.1 (PWR), U19.1 (PWR), U21.8 (VCC2), U22.8 (VCC2), U24.4 (V+), U25.1 (VDD), U26.22 (5V_OPT); also elsewhere on the board
/APPS_1_Raw: U17.3 (Out1), U24.10 (+); also elsewhere on the board
/APPS_2_Raw: U18.3 (Out1), U24.12 (+); also elsewhere on the board
/BPPS_1_Raw: U19.3 (Out1), U24.3 (+); also elsewhere on the board
/Brake_LED_Cathode: D21.1 (K), Q9.3 (D); also elsewhere on the board
/CAN_Powertrain_H: R63.2, U21.6 (CANH); also elsewhere on the board
/CAN_Powertrain_L: R63.1, U21.5 (CANL); also elsewhere on the board
/Dash_Lap: R65.1, R67.2; also elsewhere on the board
/Dash_Launch: R64.1, R66.2; also elsewhere on the board
/Driverless_Signal: R68.1, R70.2; also elsewhere on the board
/MCU/BOOT0: R73.1, U27.60 (BOOT0)
/MCU/BOOT1: R80.1, U27.28 (PB2)
/MCU/BSDP_Fault: R87.1; also elsewhere on the board
/MCU/BSPD_Fault_3V3: R87.2, R88.1, U27.16 (PA2)
/MCU/BSPD_Shutdown_Out_3V04: R82.1, R84.2, U27.17 (ADC1_IN3)
/MCU/Front_Brake_Buff_Filtered_3V: R85.2, R86.2, U27.15 (ADC1_IN1)
/MCU/OSC_IN: C37.1, U27.5 (RCC_OSC_IN), Y1.3
/MCU/OSC_OUT: C38.1, U27.6 (RCC_OSC_OUT), Y1.1
/MCU/Rear_Brake_Buff_Filtered_3V: R81.2, R83.2, U27.14 (ADC1_IN0)
/MCU/SPS_1_Raw: RV3.2, U24.5 (+); also elsewhere on the board
/MCU/Solenoid_Neg: D24.1 (K), Q10.2 (S); also elsewhere on the board
/MCU/Status_Indicator_Strip_3V: Q6.2 (S), R72.1, U27.3 (PC14)
/RTD_Button_Neg: R53.1, R54.1, SW4.1; also elsewhere on the board
/RTD_Buzzer_Neg: LS1.N, Q8.3 (D); also elsewhere on the board
/RTD_Buzzer_Pos: LS1.P, R79.1; also elsewhere on the board
/RTD_LED_Cathode: D20.1 (K), Q7.3 (D); also elsewhere on the board
/Status_Indicator_Strip: Q6.3 (D), R71.2, U25.4 (DIN); also elsewhere on the board
/UART5_RX: U27.54 (UART5_RX); also elsewhere on the board
/UART5_TX: U27.53 (UART5_TX); also elsewhere on the board
APPS_1_Buff_Filt: C28.1, R55.1, R56.1, U27.9 (ADC1_IN11)
APPS_2_Buff_Filt: C29.1, R57.2, R58.2, U27.10 (ADC1_IN12)
BME_NSS: U27.56 (SPI2_NSS); also elsewhere on the board
BNO_BOOTN: U27.40 (PC9); also elsewhere on the board
BNO_NRST: U27.39 (PC8); also elsewhere on the board
BPPS_1_Buff_Filt: C30.1, R59.1, R60.1, U27.11 (ADC1_IN13)
BSPD_Shutdown_Out: R84.1; also elsewhere on the board
Brake_Light_Signal: R76.2, R78.1, U27.24 (PC4)
CAN_Data_H: R62.2, U22.6 (CANH); also elsewhere on the board
CAN_Data_L: R62.1, U22.5 (CANL); also elsewhere on the board
CAN_Data_RX: U22.3 (RXD), U27.57 (CAN2_RX)
CAN_Data_TX: U22.2 (TXD), U27.58 (CAN2_TX)
CAN_Powertrain_RX: U21.3 (RXD), U27.61 (CAN1_RX)
CAN_Powertrain_TX: U21.2 (TXD), U27.62 (CAN1_TX)
Dash_Lap_Filtered: C36.1, R67.1, U27.21 (PA5)
Dash_Launch_Filtered: C35.1, R66.1, U27.20 (PA4)
Driverless_Signal_Filtered: C39.1, R70.1, U27.22 (PA6)
Front_Brake_Buff_Filtered: R86.1; also elsewhere on the board
GND: C23.2, C25.2, C26.2, C27.2, C28.2, C29.2, C30.2, C33.2, C34.2, C35.2, C36.2, C37.2, C38.2, C39.2, C40.1, C41.1, C42.1, C43.2, C44.2, C45.2, C46.2, C47.2, C48.2, C49.2, D19.1 (K), D24.2 (A), J4.5, J4.7, J4.11, Q7.2 (S), Q8.2 (S), Q9.2 (S), Q10.3 (D), R53.2, R56.2, R58.1, R60.2, R64.2, R65.2, R68.2, R73.2, R75.1, R76.1, R80.2, R81.1, R82.2, R85.1, R88.2, R90.1, R92.2, RV3.3, SW5.1, U17.2 (GND), U18.2 (GND), U19.2 (GND), U21.4 (GND1), U21.7 (GND2), U22.4 (GND1), U22.7 (GND2), U24.11 (V-), U25.2 (VSS), U25.3 (BIN), U26.5 (GNDDETECT), U26.8 (GND_2), U26.24 (GND), U26.26 (GND2), U26.27 (GND3), U26.29 (GND4), U27.12 (VSSA), U27.18 (VSS), U27.31 (VSS), U27.47 (VSS), U27.63 (VSS), Y1.2, Y1.4; also elsewhere on the board
INT1_3V3: U27.34 (PB13); also elsewhere on the board
NRST: C40.2, J4.12, SW5.2, U26.31 (T_NRST), U27.7 (NRST)
unnamed: D19.2 (A), R69.1
unnamed: D20.2 (A), D21.2 (A)
unnamed: Q7.1 (G), R61.1
unnamed: Q8.1 (G), R77.2
unnamed: Q9.1 (G), R78.2
unnamed: Q10.1 (G), R74.1
unnamed: R59.2, U24.1, U24.2 (-)
unnamed: R91.2, U24.6 (-), U24.7
unnamed: R55.2, U24.8, U24.9 (-)
unnamed: R57.1, U24.13 (-), U24.14
unnamed: TP11.1, U27.41 (PA8)
unnamed: TP12.1, U27.42 (PA9)
unnamed: TP13.1, U27.43 (PA10)
unnamed: TP21.1, U27.45 (PA12)
unnamed: TP17.1, U27.50 (PA15)
unnamed: TP14.1, U27.26 (PB0)
unnamed: TP18.1, U27.59 (PB7)
unnamed: TP15.1, U27.29 (PB10)
unnamed: TP16.1, U27.4 (PC15)
unnamed: C41.2, U27.30 (VCAP_1)
RTD_Button_3V3: C27.1, R54.2, U27.2 (PC13)
RTD_Buzzer: R75.2, R77.1, U27.23 (PA7)
RTD_LED: R61.2, R69.2, U27.8 (PC0)
Rear_Brake_Buff_Filtered: R83.1; also elsewhere on the board
SPI2_MISO: U27.35 (SPI2_MISO); also elsewhere on the board
SPI2_MOSI: U27.36 (SPI2_MOSI); also elsewhere on the board
SPI2_NSS: U27.33 (SPI2_NSS); also elsewhere on the board
SPI2_SCK: U27.38 (SPI2_SCK); also elsewhere on the board
SPS_1_Buff_Filt: C23.1, R91.1, R92.1, U27.25 (PC5)
STLINK_SWCLK: J4.6, U26.13 (T_JCLK/T_SWCLK), U27.49 (SYS_JTCK-SWCLK)
STLINK_SWDIO: J4.4, U26.4 (T_JTMS/T_SWDIO), U27.46 (SYS_JTMS-SWDIO)
STLINK_SWO: J4.8, U26.6 (T_JTDO/T_SWO), U27.55 (SYS_JTDO-SWO)
Solenoid_Signal: R74.2, R90.2, U27.27 (PB1)
UART4_RX: J4.13, U26.15 (T_VCP_RX), U27.52 (UART4_RX)
UART4_TX: J4.14, U26.12 (T_VCP_TX), U27.51 (UART4_TX)
WKUP1: U27.44 (PA11); also elsewhere on the board

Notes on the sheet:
3.3V
(12k + 20k)/(2π*12k*20k*39*10^-9) = 544.119 HZ
1/(2pi*100000*40*10^-9) = 39.79 HZ
STLINKV3-MODS Programmer
RED LED STRIP
0-3.125 V
0-1.875 V
Dash Pins
CAN Tranceiver
Brake Light Logic
4.5 V
5V Max
0-3.0 V Analog
Green
ST-Link Programming/Debugging Connector
(12k + 20k)/(2π*12k*20k*220*10^-9) = 96.458 HZ
Regenerative Braking Solenoid
NOTE: CAN Bridge left disconnected for now, but if we can figure out the protocol on the usb side to access it, we can connect it
79.98 DBA at 2m (Cole Wanted Quieter) 3,800 ± 500 Hz Resonant Frequency
1/(2pi*300000*4.7*10^-9) = 112.88 HZ
5V Max
APPS + BPPS Buffer + Filter
5 V
Power Supply
14V
Gain: 0.217 * Voltage input 0 to 3.04V Max given 14v input
Microcontroller

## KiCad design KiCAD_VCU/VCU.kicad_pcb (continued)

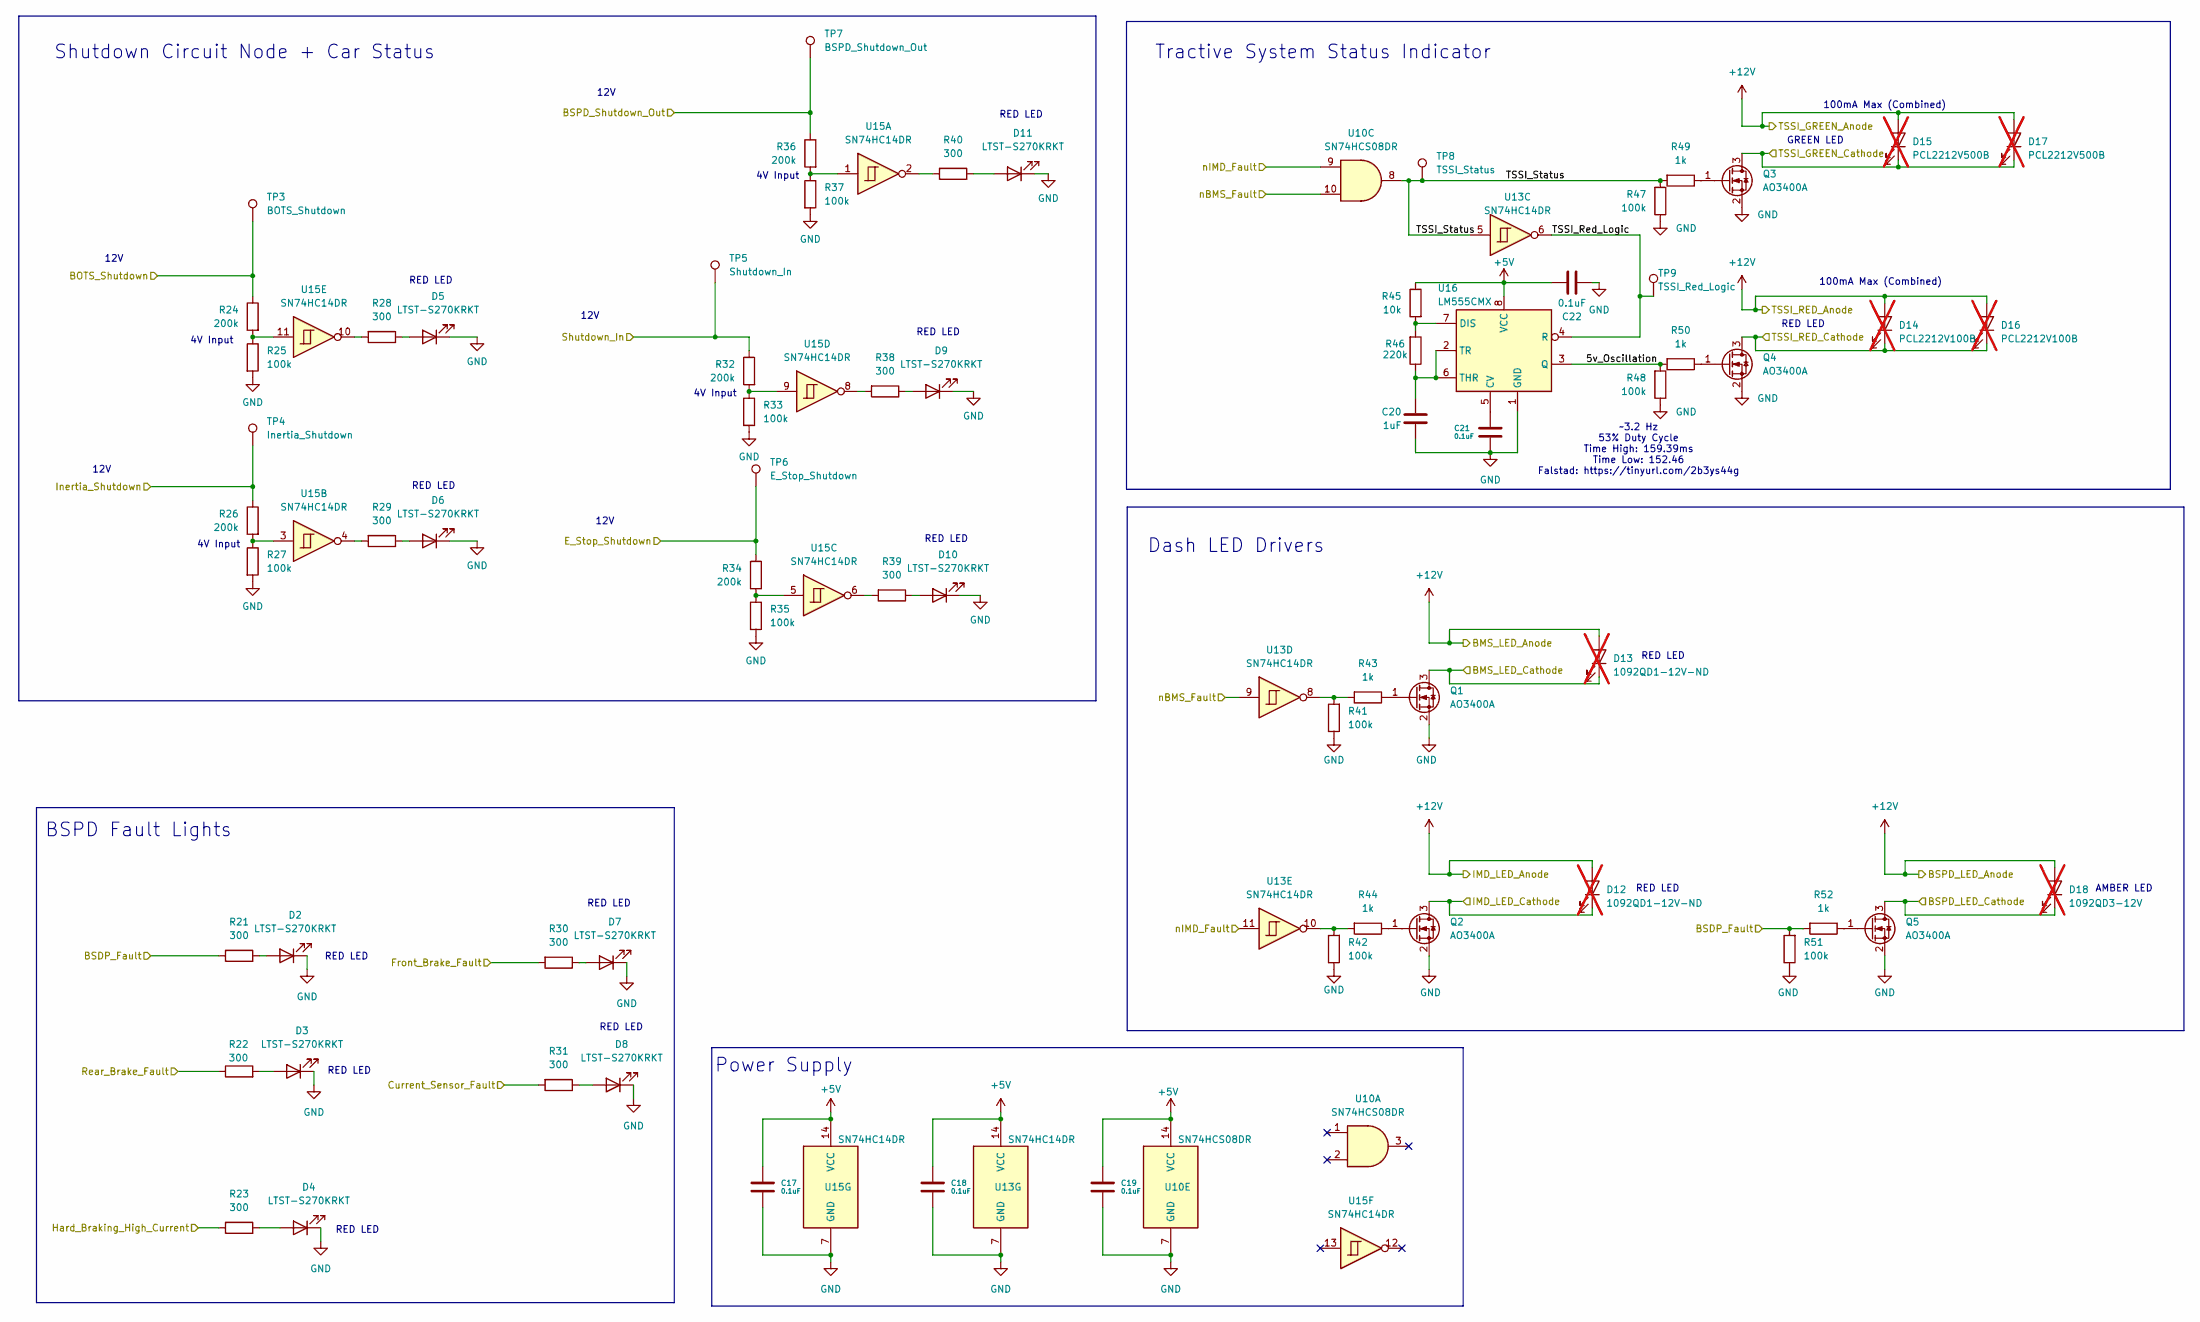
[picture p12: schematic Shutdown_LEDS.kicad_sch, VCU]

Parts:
C17, C18, C19, C21, C22: 0.1uF; C_0603_1608Metric_Pad1.08x0.95mm_HandSolder; MFG PN CC0603JRX7R9BB104; Digi PN 311-1779-1-ND
C20: 1uF; C_0603_1608Metric_Pad1.08x0.95mm_HandSolder; MFG PN CC0603JRX7R6BB105; Digi PN 311-3484-1-ND
D2, D3, D4, D5, D6, D7, D8, D9, D10, D11: LTST-S270KRKT; LED_0603_1608Metric_Pad1.05x0.95mm_HandSolder; MFG PN LTST-S270KRKT; Digi PN 160-1479-1-ND
D12, D13: 1092QD1-12V-ND; MFG PN 1092QD1-12V; Digi PN 1092QD1-12V-ND; not fitted
D14, D16: PCL2212V100B; MFG PN PCL2212V100B; Digi PN PCL2212V100B-ND; not fitted
D15, D17: PCL2212V500B; MFG PN PCL2212V500B; Digi PN PCL2212V500B-ND; not fitted
D18: 1092QD3-12V; MFG PN 1092QD3-12V; Digi PN 1092QD3-12V-ND; not fitted
Q1, Q2, Q3, Q4, Q5: AO3400A; SOT-23; MFG PN AO3400A; Digi PN 785-1000-1-ND
R21, R22, R23, R28, R29, R30, R31, R38, R39, R40: 300; R_0603_1608Metric_Pad0.98x0.95mm_HandSolder; MFG PN AC0603FR-07300RL; Digi PN YAG5330CT-ND
R24, R26, R32, R34, R36: 200k; R_0603_1608Metric_Pad0.98x0.95mm_HandSolder; MFG PN AC0603FR-07200KL; Digi PN YAG3575CT-ND
R25, R27, R33, R35, R37, R41, R42, R47, R48, R51: 100k; R_0603_1608Metric_Pad0.98x0.95mm_HandSolder; MFG PN AC0603FR-13100KL; Digi PN 13-AC0603FR-13100KLCT-ND
R43, R44, R49, R50, R52: 1k; R_0603_1608Metric_Pad0.98x0.95mm_HandSolder; MFG PN RC0603FR-071KL; Digi PN 311-1.00KHRCT-ND
R45: 10k; R_0603_1608Metric_Pad0.98x0.95mm_HandSolder; MFG PN AC0603FR-0710KL; Digi PN 311-10KLDCT-ND
R46: 220k; R_0603_1608Metric_Pad0.98x0.95mm_HandSolder; MFG PN AC0603FR-07220KL; Digi PN YAG3579CT-ND
TP3: BOTS_Shutdown; TestPoint_Pad_D1.0mm
TP4: Inertia_Shutdown; TestPoint_Pad_D1.0mm
TP5: Shutdown_In; TestPoint_Pad_D1.0mm
TP6: E_Stop_Shutdown; TestPoint_Pad_D1.0mm
TP7: BSPD_Shutdown_Out; TestPoint_Pad_D1.0mm
TP8: TSSI_Status; TestPoint_Pad_D1.0mm
TP9: TSSI_Red_Logic; TestPoint_Pad_D1.0mm
U10: SN74HCS08DR; SOIC-14_3.9x8.7mm_P1.27mm; MFG PN SN74HCS08DR; Digi PN 296-SN74HCS08DRCT-ND
U13, U15: SN74HC14DR; SOIC-14_3.9x8.7mm_P1.27mm; MFG PN SN74HC14DR; Digi PN 296-1194-1-ND
U16: LM555CMX; SOIC-8_3.9x4.9mm_P1.27mm; MFG PN LM555CMX/NOPB; Digi PN LM555CMX/NOPBCT-ND

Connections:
+5V: C17.1, C18.1, C19.1, C22.1, R45.1, U10.14 (VCC), U13.14 (VCC), U15.14 (VCC), U16.8 (VCC); also elsewhere on the board
/BMS_LED_Cathode: D13.1 (K), Q1.3 (D); also elsewhere on the board
/BSPD_LED_Cathode: D18.1 (K), Q5.3 (D); also elsewhere on the board
/IMD_LED_Cathode: D12.1 (K), Q2.3 (D); also elsewhere on the board
/MCU/BSDP_Fault: R21.2, R51.2, R52.2; also elsewhere on the board
/Shutdown_VCU/Shutdown_LEDS/5v_Oscillation: R48.2, R50.2, U16.3 (Q)
/Shutdown_VCU/Shutdown_LEDS/TSSI_Red_Logic: TP9.1, U13.6, U16.4 (R)
/Shutdown_VCU/Shutdown_LEDS/TSSI_Status: R47.2, R49.2, TP8.1, U10.8, U13.5
/TSSI_GREEN_Cathode: D15.1 (K), D17.1 (K), Q3.3 (D); also elsewhere on the board
/TSSI_RED_Cathode: D14.1 (K), D16.1 (K), Q4.3 (D); also elsewhere on the board
/nBMS_Fault: U10.10, U13.9; also elsewhere on the board
/nIMD_Fault: U10.9, U13.11; also elsewhere on the board
BOTS_Shutdown: R24.1, TP3.1; also elsewhere on the board
BSPD_Shutdown_Out: R36.1, TP7.1; also elsewhere on the board
Current_Sensor_Fault: R31.2; also elsewhere on the board
E_Stop_Shutdown: R34.1, TP6.1; also elsewhere on the board
Front_Brake_Fault: R30.2; also elsewhere on the board
GND: C17.2, C18.2, C19.2, C20.1, C21.1, C22.2, D2.1 (K), D3.1 (K), D4.1 (K), D5.1 (K), D6.1 (K), D7.1 (K), D8.1 (K), D9.1 (K), D10.1 (K), D11.1 (K), Q1.2 (S), Q2.2 (S), Q3.2 (S), Q4.2 (S), Q5.2 (S), R25.2, R27.2, R33.2, R35.2, R37.2, R41.1, R42.1, R47.1, R48.1, R51.1, U10.7 (GND), U13.7 (GND), U15.7 (GND), U16.1 (GND); also elsewhere on the board
Hard_Braking_High_Current: R23.2; also elsewhere on the board
Inertia_Shutdown: R26.1, TP4.1; also elsewhere on the board
unnamed: D2.2 (A), R21.1
unnamed: D3.2 (A), R22.2
unnamed: D4.2 (A), R23.1
unnamed: D5.2 (A), R28.1
unnamed: D6.2 (A), R29.1
unnamed: D7.2 (A), R30.1
unnamed: D8.2 (A), R31.1
unnamed: D9.2 (A), R38.1
unnamed: D10.2 (A), R39.1
unnamed: D11.2 (A), R40.1
unnamed: D12.2 (A), D13.2 (A), D14.2 (A), D15.2 (A), D16.2 (A), D17.2 (A), D18.2 (A)
unnamed: Q1.1 (G), R43.1
unnamed: Q2.1 (G), R44.1
unnamed: Q3.1 (G), R49.1
unnamed: Q4.1 (G), R50.1
unnamed: Q5.1 (G), R52.1
unnamed: R24.2, R25.1, U15.11
unnamed: R26.2, R27.1, U15.3
unnamed: R28.2, U15.10
unnamed: R29.2, U15.4
unnamed: R32.2, R33.1, U15.9
unnamed: R34.2, R35.1, U15.5
unnamed: R36.2, R37.1, U15.1
unnamed: R38.2, U15.8
unnamed: R39.2, U15.6
unnamed: R40.2, U15.2
unnamed: R41.2, R43.2, U13.8
unnamed: R42.2, R44.2, U13.10
unnamed: C21.2, U16.5 (CV)
unnamed: R45.2, R46.2, U16.7 (DIS)
unnamed: C20.2, R46.1, U16.2 (TR), U16.6 (THR)
Rear_Brake_Fault: R22.1; also elsewhere on the board
Shutdown_In: R32.1, TP5.1; also elsewhere on the board

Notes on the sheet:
4V Input
12V
RED LED
~3.2 Hz 53% Duty Cycle Time High: 159.39ms Time Low: 152.46 Falstad: https://tinyurl.com/2b3ys44g
BSPD Fault Lights
Shutdown Circuit Node + Car Status
Power Supply
GREEN LED
AMBER LED
Tractive System Status Indicator
100mA Max (Combined)
100mA Max (Combined)
Dash LED Drivers

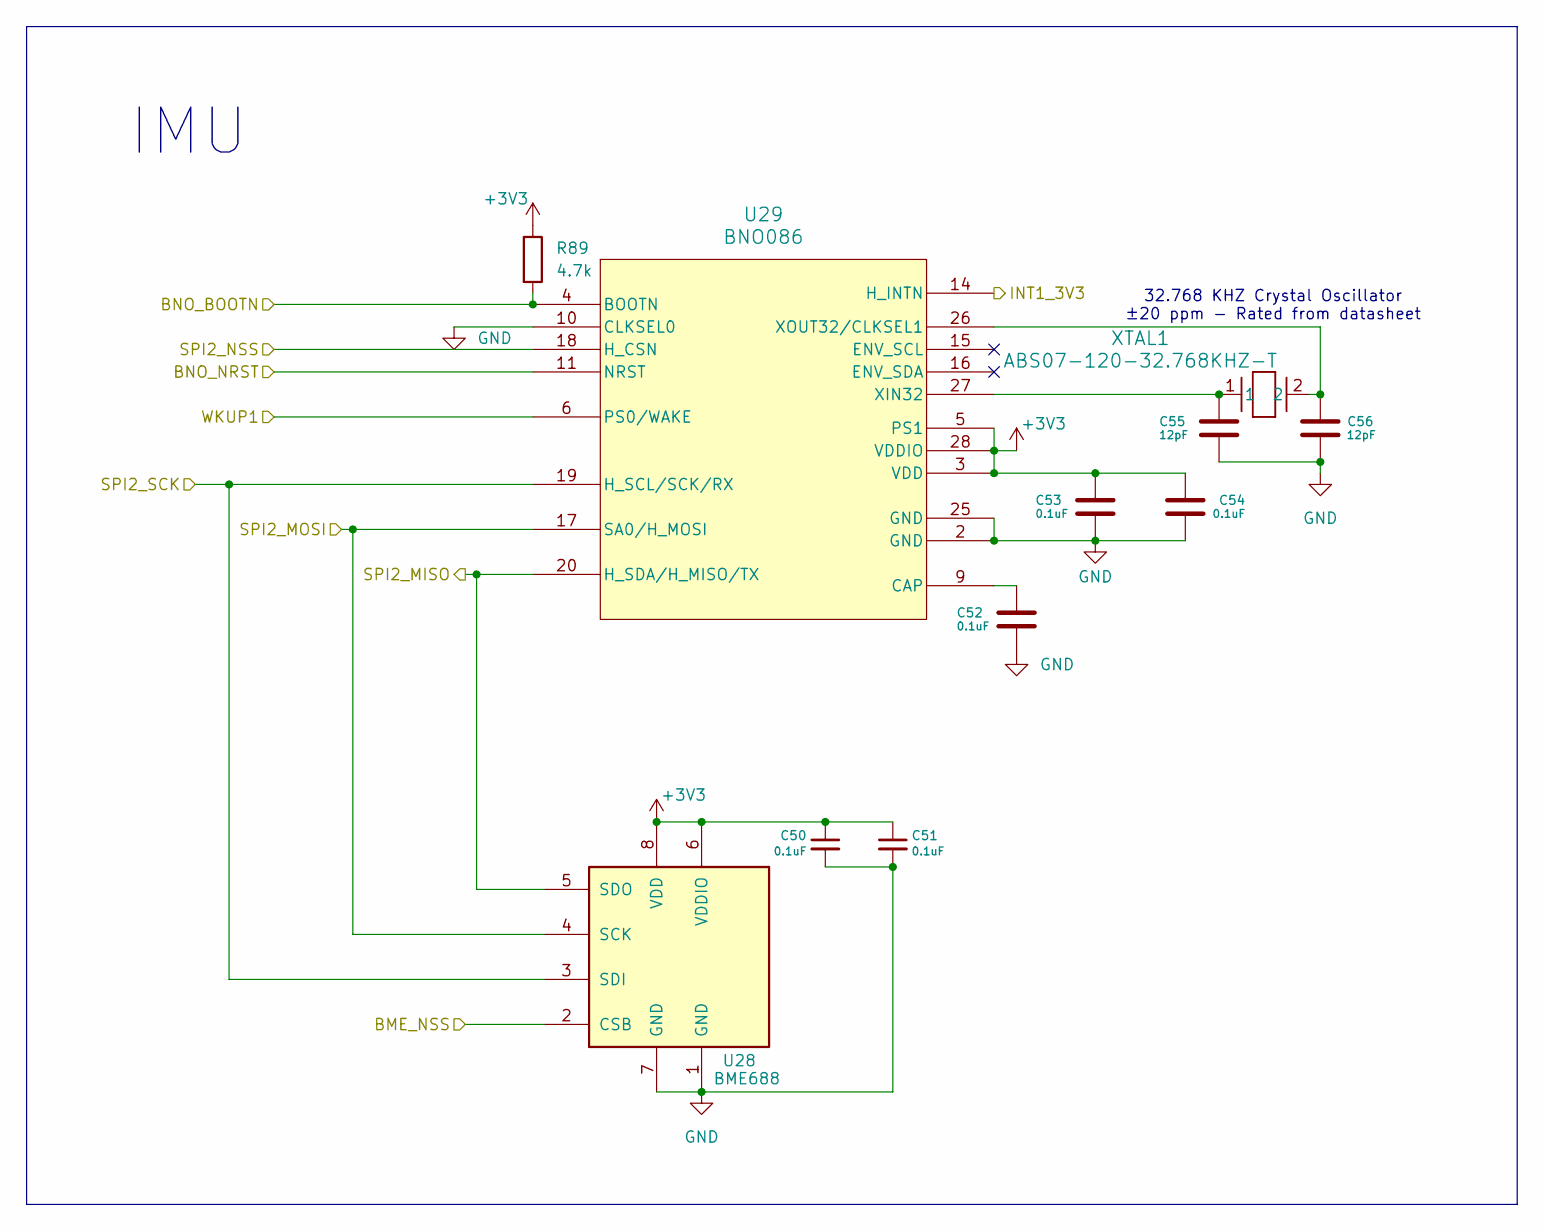
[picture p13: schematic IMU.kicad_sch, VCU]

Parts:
C50, C51, C52, C53, C54: 0.1uF; C_0603_1608Metric_Pad1.08x0.95mm_HandSolder; MFG PN CC0603JRX7R9BB104; Digi PN 311-1779-1-ND
C55, C56: 12pF; C_0603_1608Metric_Pad1.08x0.95mm_HandSolder; MFG PN CC0603FRNPO9BN120; Digi PN 311-3885-1-ND
R89: 4.7k; R_0603_1608Metric_Pad0.98x0.95mm_HandSolder; MFG PN AC0603FR-074K7L; Digi PN YAG3613CT-ND
U28: BME688; BME_688_Bosch_LGA-8_3x3mm_P0.8mm_ClockwisePinNumbering; PARTREV 1.0; Digi PN 828-BME688CT-ND
U29: BNO086; BNO086_LGA-28_5.2x3.8mm_P0.5mm; MFG PN BNO086; Digi PN 1888-BNO086CT-ND
XTAL1: ABS07-120-32.768KHZ-T; Crystal_SMD_EuroQuartz_EQ161-2Pin_3.2x1.5mm_HandSoldering; MFG PN ABS07-32.768KHZ-T; Digi PN 535-9542-1-ND

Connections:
+3V3: C50.1, C51.1, C53.2, C54.2, R89.1, U28.6 (VDDIO), U28.8 (VDD), U29.3 (VDD), U29.5 (PS1), U29.28 (VDDIO); also elsewhere on the board
BME_NSS: U28.2 (CSB); also elsewhere on the board
BNO_BOOTN: R89.2, U29.4 (BOOTN); also elsewhere on the board
BNO_NRST: U29.11 (NRST); also elsewhere on the board
GND: C50.2, C51.2, C52.1, C53.1, C54.1, C55.1, C56.1, U28.1 (GND), U28.7 (GND), U29.2 (GND), U29.10 (CLKSEL0), U29.25 (GND); also elsewhere on the board
INT1_3V3: U29.14 (H_INTN); also elsewhere on the board
unnamed: C52.2, U29.9 (CAP)
unnamed: C55.2, U29.27 (XIN32), XTAL1.1
unnamed: C56.2, U29.26 (XOUT32/CLKSEL1), XTAL1.2
SPI2_MISO: U28.5 (SDO), U29.20 (H_SDA/H_MISO/TX); also elsewhere on the board
SPI2_MOSI: U28.4 (SCK), U29.17 (SA0/H_MOSI); also elsewhere on the board
SPI2_NSS: U29.18 (H_CSN); also elsewhere on the board
SPI2_SCK: U28.3 (SDI), U29.19 (H_SCL/SCK/RX); also elsewhere on the board
WKUP1: U29.6 (PS0/WAKE); also elsewhere on the board

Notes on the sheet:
32.768 KHZ Crystal Oscillator ±20 ppm - Rated from datasheet
IMU

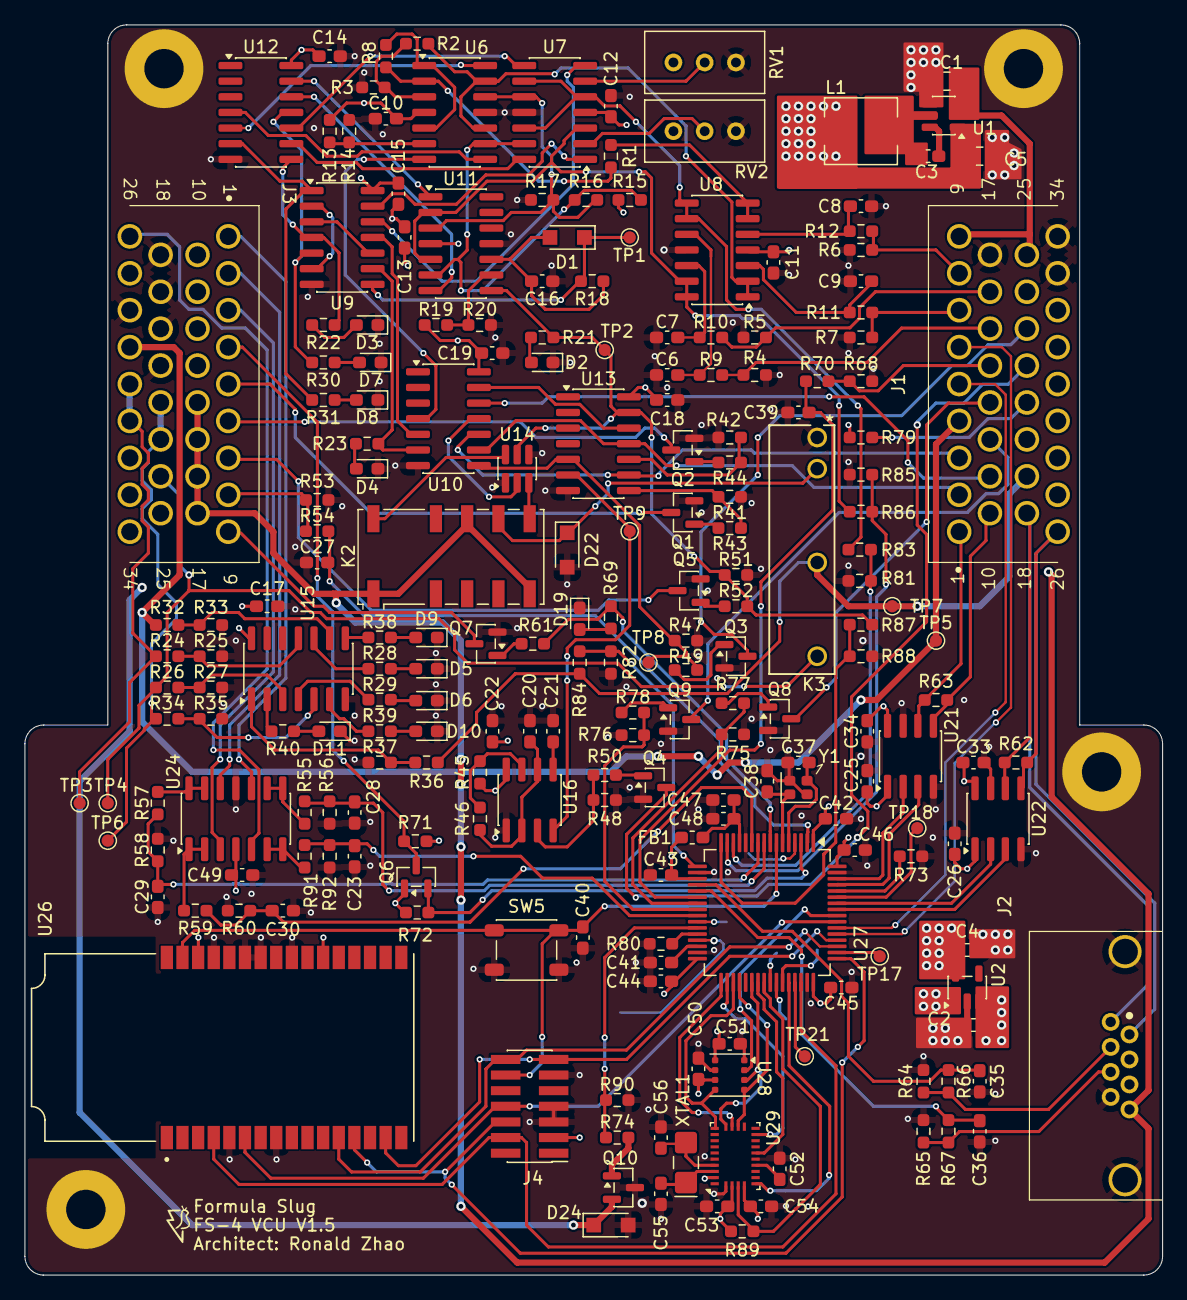
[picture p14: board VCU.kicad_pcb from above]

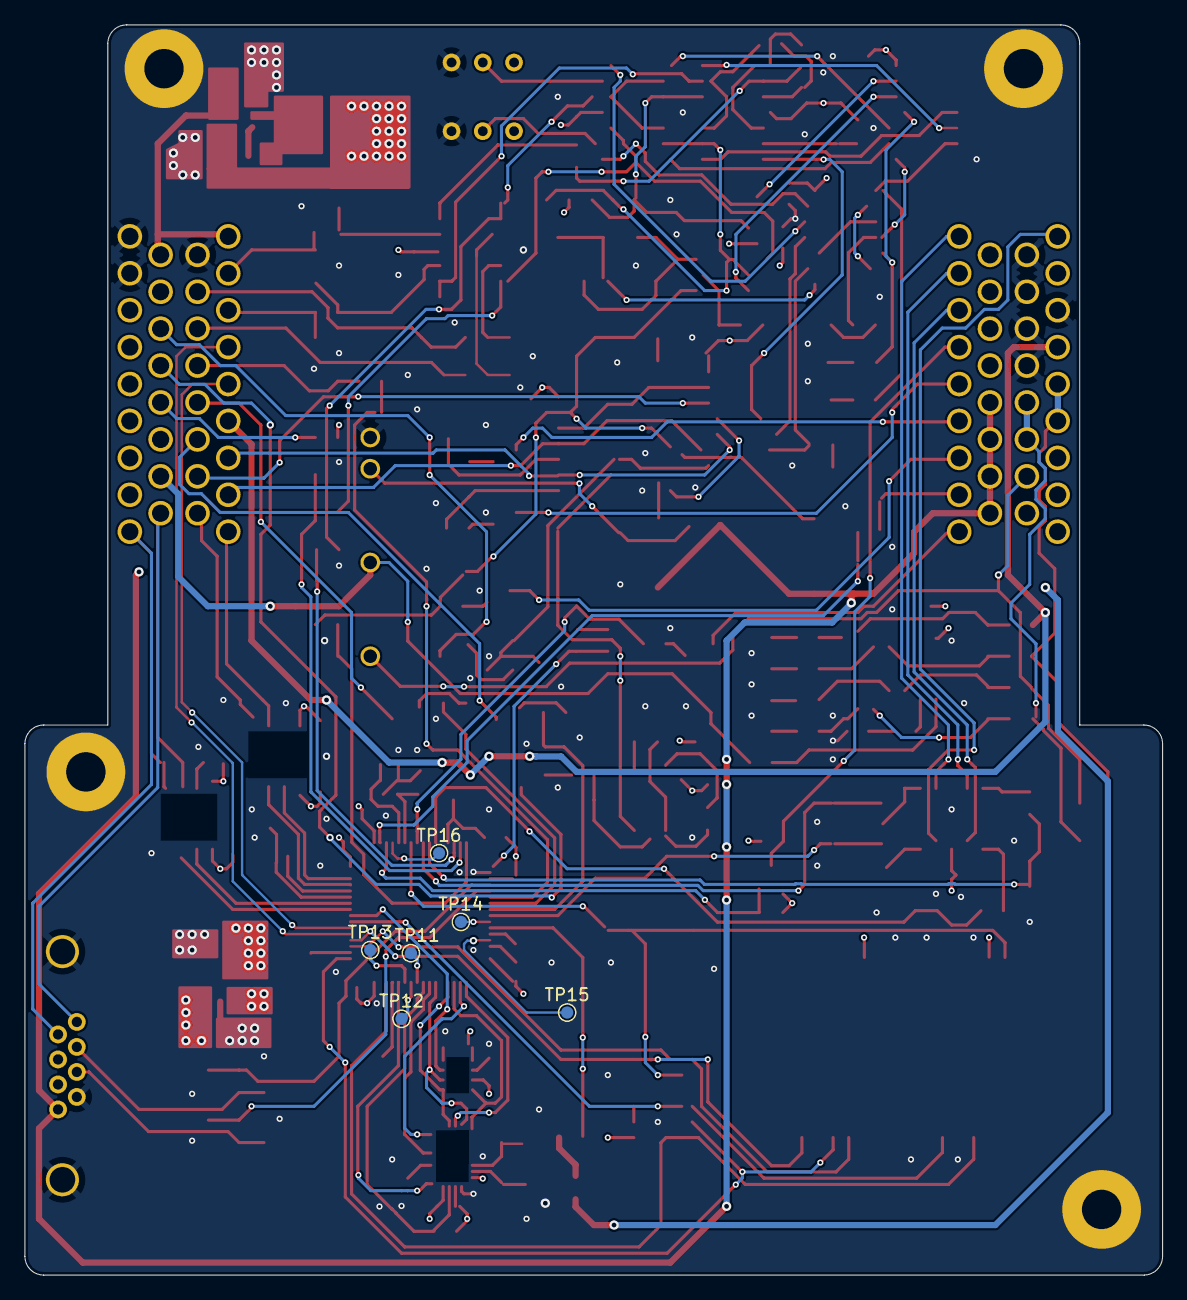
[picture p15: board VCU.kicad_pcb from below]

Board: 4 copper layers, 92.5 x 101.6 mm, 224 parts (6 on the bottom side), 180 nets.

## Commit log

2026-04-07 Updated README.md
    Added a brief overview of the pcb
2026-04-07 Images for schematic
2026-04-07 Updated IMU image
2026-04-07 Added Soldering Image
2026-04-07 KiCad Schematics + PCB
    [IMU.kicad_sch, MCU.kicad_sch, Shutdown_LEDS.kicad_sch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]
